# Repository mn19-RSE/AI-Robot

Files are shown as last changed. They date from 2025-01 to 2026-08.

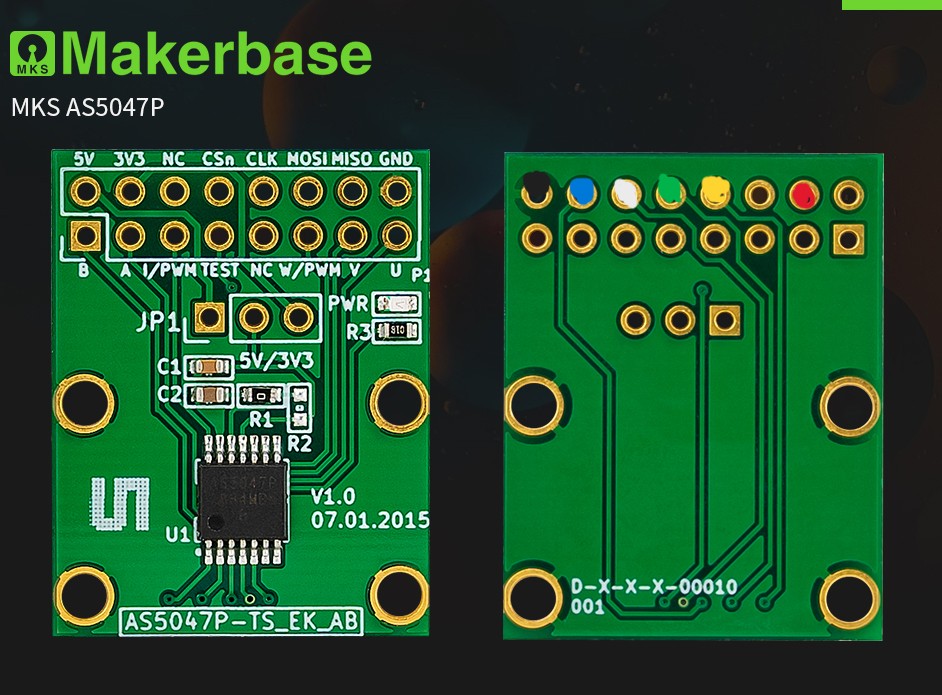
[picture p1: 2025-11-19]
hardware/reference_images/AS5047P Image.jpg

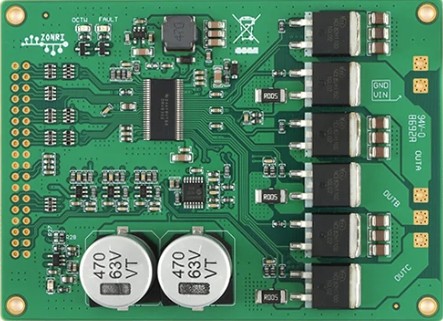
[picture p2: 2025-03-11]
hardware/reference_images/DRV8302_Top_View_Image.jpg

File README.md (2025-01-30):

# AI-Robot
This is a repo representing the personal robotics project I started in late 2024.  
The plan is to create a walking robot that will incorporate BLDC motors, CAN bus communication, machine vision, and AI models for object detection and decision making.

## License
This project is protected under the defualt copyright laws. I retain all rights to the source code created by me and no one may reproduce, distribute, or create derivative original works from this project.

## Contained Files
- 3D CAD models
- Arduino code for motion control
- ML code for machine vision and decisinon making 
- BOM

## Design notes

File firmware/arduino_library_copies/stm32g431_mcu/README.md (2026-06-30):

# STM32G431 MCU Header file library
Pin definitions for the BLDC complete drive controller that uses the STM32G431 microcontorller. SPI pins, driver PWM and enebale pins, and the CAN pins are defined to make it easier to call functions in the .ino file.

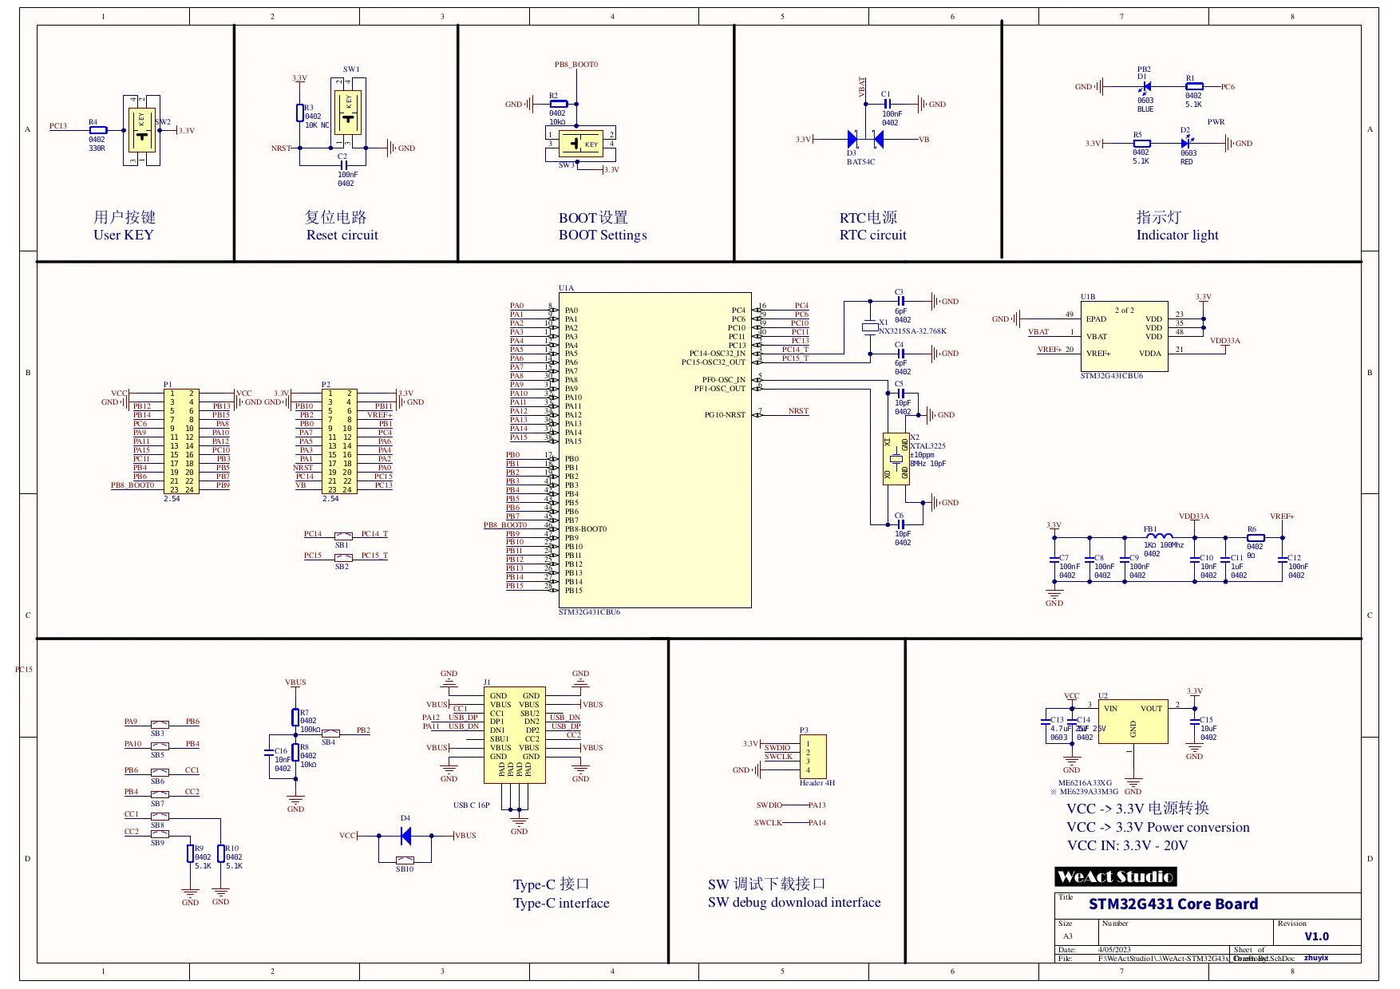
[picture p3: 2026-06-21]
hardware/electrical_documentation/schematics/WeAct-STM32G4-schematics.jpg

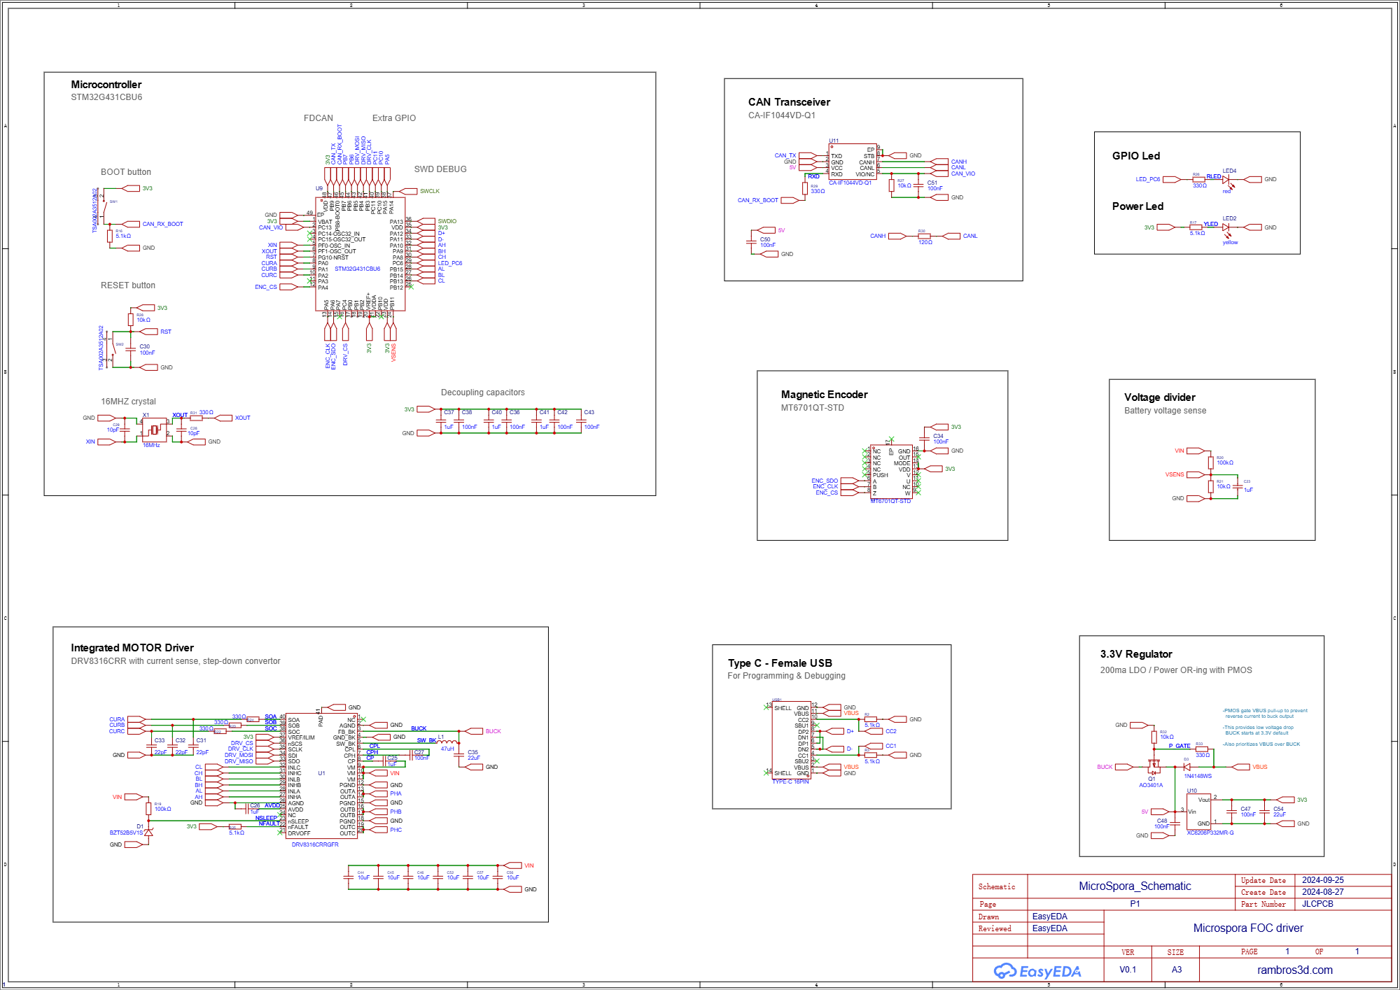
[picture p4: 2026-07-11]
hardware/electrical_documentation/schematics/SCH_MIcroSpora_DRV8316.png

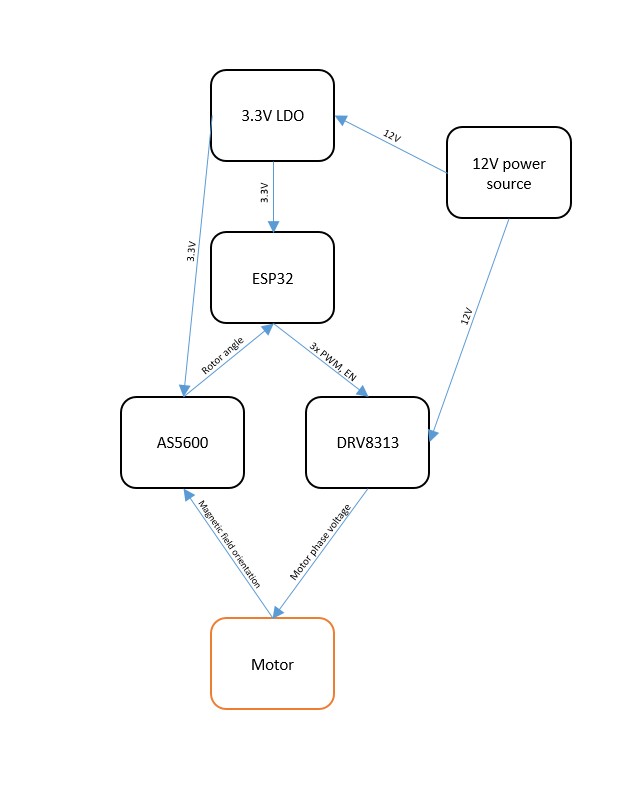
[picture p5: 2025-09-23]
hardware/reference_images/AIO_ESP32_DRV8313_AS5600_block_diagram.jpg

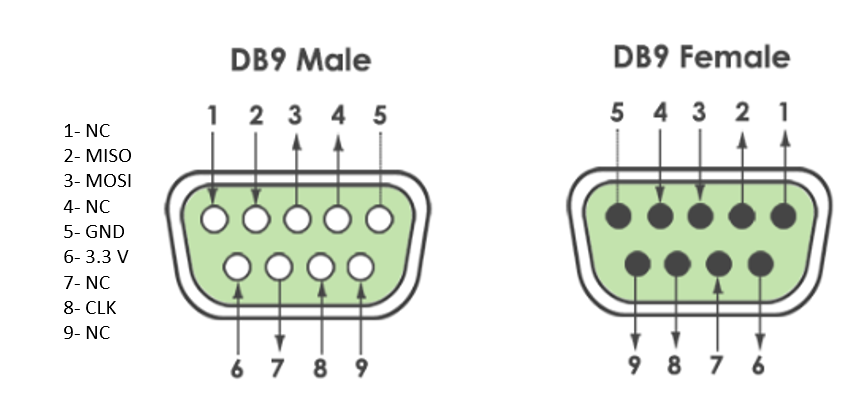
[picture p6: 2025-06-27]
hardware/reference_images/DB9 AS5047p Pinout.png

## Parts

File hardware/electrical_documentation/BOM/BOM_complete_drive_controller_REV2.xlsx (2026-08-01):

No. | Quantity | Comment | Designator | Footprint | Value | Manufacturer Part | Supplier Part | Category | Device
1 | 10 | 100nF | C1,C2,C3,C4,C5,C6,C7,C8,C9,C14 | C0402 | 100nF |  | C1525 | Capacitors:Multilayer Ceramic Capacitors MLCC - SMD/SMT | CAP_0402
2 | 4 | 100nF | C10,C11,C12,C15 | C0603 | 100nF |  |  | Capacitors:Multilayer Ceramic Capacitors MLCC - SMD/SMT | CAP_0603
3 | 1 | 47nF | C13 | C0603 | 47nF |  |  | Capacitors:Multilayer Ceramic Capacitors MLCC - SMD/SMT | CAP_0603
4 | 1 | 100nF | C16 | C0603 | 100nF | CC0603KRX7R9BB104 | C14663 | Capacitors:Multilayer Ceramic Capacitors MLCC - SMD/SMT | CC0603KRX7R9BB104
5 | 1 | 10uF | C17 | C0402 | 10uF | CL05A106MQ5NUNC | C15525 | Capacitors:Multilayer Ceramic Capacitors MLCC - SMD/SMT | CL05A106MQ5NUNC
6 | 1 | 22uF | Cbk | C0402 | 22uF |  |  | Capacitors:Multilayer Ceramic Capacitors MLCC - SMD/SMT | CAP_0402
7 | 1 | SMBJ12A | D1 | SMB_L4.6-W3.6-LS5.3-RD |  | SMBJ12A | C127552 |  | SMBJ12A
8 | 1 | HDR-M_2.54_1x2P | H1 | HDR-TH_2P-P2.54-V-M-1 |  |  |  | Connectors:Pin Headers | HDR-M_2.54_1x2P
9 | 1 | 47uH | Lbk | L0805 | 47uH |  |  | Inductors/Coils/Transformers:Inductors (SMD) | L_0805
10 | 2 | 10K | R2,R5 | R0603 | 10K |  |  | Resistors:Chip Resistor - Surface Mount | Res_0603
11 | 1 | 5.1K | R6 | R0402 | 5.1K |  |  | Resistors:Chip Resistor - Surface Mount | Res_0402
12 | 1 | 47K | R7 | R0402 | 47K |  |  | Resistors:Chip Resistor - Surface Mount | Res_0402
13 | 1 | 10kΩ | R8 | R0603 | 10kΩ | 0603WAF1002T5E | C25804 | Resistors:Chip Resistor - Surface Mount | 0603WAF1002T5E
14 | 2 | 5.1K | R9,R10 | R0603 | 5.1K |  |  | Resistors:Chip Resistor - Surface Mount | Res_0603
15 | 1 | 120 | RCAN | R0603 | 120 |  |  | Resistors:Chip Resistor - Surface Mount | Res_0603
16 | 2 | 95c04a3gwrt | S1,S2 | 95C04A3GWRT | 95C04A3GWRT |  |  |  | 95c04a3gwrt
17 | 1 | STM32G431CBT6 | U2 | LQFP-48_L7.0-W7.0-P0.50-LS9.0-BL |  | STM32G431CBT6 | C529355 | Embedded Processors & Controllers:Microcontrollers (MCU/MPU/SOC) | STM32G431CBT6
18 | 1 | DRV8316CTRGFR | U3 | VQFN-40_L7.0-W5.0-P0.50-TL-EP5.7 |  | DRV8316CTRGFR | C6602057 | Motor Driver ICs:Brushless DC (BLDC) Motor Driver | DRV8316CTRGFR
19 | 1 | aha0608470m035r | U4 | CAPAE660X850N |  |  |  |  | aha0608470m035r
20 | 1 | AS5048A-HTSP-500 | U5 | TSSOP-14_L5.0-W4.4-P0.65-LS6.4-BL |  | AS5048A-HTSP-500 | C2655181 | Sensors:Position Sensors | AS5048A-HTSP-500
21 | 1 | XT30(2+2) | U6 | CONN-TH_XT30-2-2 |  | XT30(2+2) | C9900178769 |  | XT30(2+2)
22 | 1 | CONN_03_POS_SCREW_3.5MM | U7 | SCREWTERMINAL-3.5MM-3 |  |  |  |  | CONN_03_POS_SCREW_3.5MM
23 | 1 | TCAN3413DR | U8 | SOP-8_L4.9-W3.9-P1.27-LS6.0-BL-1 |  | TCAN3413DR | C22433320 | Interface:CAN Transceivers | TCAN3413DR
24 | 1 | USB4120-03-C | USB1 | TYPE-C-SMD_USB4120-03-C |  | USB4120-03-C | C3445864 | Connectors:USB Connectors | USB4120-03-C

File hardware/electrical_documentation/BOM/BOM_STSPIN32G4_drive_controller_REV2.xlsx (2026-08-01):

No. | Quantity | Comment | Designator | Footprint | Value | Manufacturer Part | Manufacturer | Supplier Part | Supplier | Category | Device
1 | 8 | 100nF | C1,C3,C5,C9,C11,C12,C13,C15 | C0603 | 100nF |  |  |  |  | Capacitors:Multilayer Ceramic Capacitors MLCC - SMD/SMT | CAP_0603
2 | 2 | 1uF | C2,C4 | C0603 | 1uF |  |  |  |  | Capacitors:Multilayer Ceramic Capacitors MLCC - SMD/SMT | CAP_0603
3 | 2 | 10uF | C6,C10 | C0603 | 10uF |  |  |  |  | Capacitors:Multilayer Ceramic Capacitors MLCC - SMD/SMT | CAP_0603
4 | 2 | 100nF | C7,C8 | C0402 | 100nF |  |  | C1525 |  | Capacitors:Multilayer Ceramic Capacitors MLCC - SMD/SMT | CAP_0402
5 | 1 | 10uF | C14 | C0603 | 10uF | CC0603KRX7R9BB104 | YAGEO(国巨) |  | LCSC | Capacitors:Multilayer Ceramic Capacitors MLCC - SMD/SMT | CC0603KRX7R9BB104
6 | 1 | 100nF | C16 | C0603 | 100nF | CC0603KRX7R9BB104 | YAGEO(国巨) | C14663 | LCSC | Capacitors:Multilayer Ceramic Capacitors MLCC - SMD/SMT | CC0603KRX7R9BB104
7 | 1 | STPS1H100A | D1 | SMA_L4.3-W2.6-LS5.2-RD |  | STPS1H100A | ST(意法半导体) | C165701 | LCSC | Diodes:Schottky Diodes | STPS1H100A
8 | 1 | HDR-M_2.54_1x2P | H1 | HDR-TH_2P-P2.54-V-M-1 |  |  |  |  |  | Connectors:Pin Headers | HDR-M_2.54_1x2P
9 | 1 | 15uH | L2 | IND-SMD_L3.8-W3.8_74406032010 | 15uH | SRR3818A-150M | BOURNS | C2045035 | LCSC | Inductors, Coils, Chokes:Power Inductors | SRR3818A-150M
10 | 3 | CSD88584Q5DC | M1,M2,M3 | SON-22_L5.0-W6.0-P0.50-CSD88599Q5DCT |  | CSD88584Q5DC | TI(德州仪器) | C2683056 | LCSC | Power Modules:DC-DC Power Modules | CSD88584Q5DC
11 | 2 | 10K | R1,R2 | R0603 | 10K |  |  |  |  | Resistors:Chip Resistor - Surface Mount | Res_0603
12 | 2 | 5.1K | R3,R4 | R0603 | 5.1K |  |  |  |  | Resistors:Chip Resistor - Surface Mount | Res_0603
13 | 6 | 4.7 | R5,R6,R7,R8,R9,R10 | R0603 | 4.7 |  |  |  |  | Resistors:Chip Resistor - Surface Mount | Res_0603
14 | 6 | 100K | R11,R12,R13,R14,R15,R16 | R0402 | 100K |  |  |  |  | Resistors:Chip Resistor - Surface Mount | Res_0402
15 | 1 | 10kΩ | R17 | R0603 | 10kΩ | 0603WAF1002T5E | UNI-ROYAL(厚声) | C25804 | LCSC | Resistors:Chip Resistor - Surface Mount | 0603WAF1002T5E
16 | 1 | 120 | RCAN | R0603 | 120 |  |  |  |  | Resistors:Chip Resistor - Surface Mount | Res_0603
17 | 2 | 95c04a3gwrt | S1,S2 | 95C04A3GWRT | 95C04A3GWRT |  |  |  |  |  | 95c04a3gwrt
18 | 1 | STSPIN32G4 | U1 | VFQFPN-64_L9.0-W9.0-P0.50-TL-EP4.0 |  | STSPIN32G4 | ST(意法半导体) | C2858620 | LCSC | Transistors/Thyristors:Intelligent Power Modules (IPM) | STSPIN32G4
19 | 1 | aha0608470m035r | U2 | CAPAE660X850N |  |  |  |  |  |  | aha0608470m035r
20 | 1 | AS5048A-HTSP-500 | U5 | TSSOP-14_L5.0-W4.4-P0.65-LS6.4-BL |  | AS5048A-HTSP-500 | ams(艾迈斯半导体) | C2655181 | LCSC | Sensors:Position Sensors | AS5048A-HTSP-500
21 | 1 | TCAN3413DR | U8 | SOP-8_L4.9-W3.9-P1.27-LS6.0-BL-1 |  | TCAN3413DR | TI(德州仪器) | C22433320 | LCSC | Interface:CAN Transceivers | TCAN3413DR
22 | 1 | USB4120-03-C | USB1 | TYPE-C-SMD_USB4120-03-C |  | USB4120-03-C | GCT | C3445864 | LCSC | Connectors:USB Connectors | USB4120-03-C

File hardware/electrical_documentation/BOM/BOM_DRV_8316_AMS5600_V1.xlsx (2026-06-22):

No. | Quantity | Comment | Designator | Footprint | Value | Manufacturer Part | Manufacturer | Supplier Part | Supplier
1 | 2 | 1uF | Ca,Cp | C0603 | 1uF
2 | 1 | 47uF | Cb | CAPAE660X850N
3 | 1 | 47nF | Cd | C0603 | 47nF
4 | 1 | 100nF | Ce | C0603 | 100nF
5 | 1 | .1uF | Cr | C0603 | .1uF
6 | 5 | 10uF | Cri,Cro,Cv0,Cv1,Cv2 | C0603 | 10uF
7 | 2 | 2.54-1*5P母 | H1,H4 | HDR-TH_5P-P2.54-V-F |  | 2.54-1*5P母 | BOOMELE(博穆精密) | C50950 | LCSC
8 | 1 | HDR-F_2.54_1x3P | H3 | HDR-TH_3P-P2.54-V-F
9 | 2 | 4.7K | R1,R2 | R0603 | 4.7K
10 | 3 | 22 | R3,R4,R5 | R0603 | 22
11 | 2 | 10K | Rf,Rm | R0603 | 10K
12 | 1 | AS5600-ASOM | U1 | SOIC127P600X175-8N
13 | 1 | ncp1117idt33t4g | U2 | NCP1117IDT33T4G
14 | 1 | DRV8316CTRGFR | U3 | VQFN-40_L7.0-W5.0-P0.50-TL-EP5.7 |  | DRV8316CTRGFR | TI(德州仪器) | C6602057 | LCSC
15 | 1 | sd12c.tct | U4 | SD12CTCT

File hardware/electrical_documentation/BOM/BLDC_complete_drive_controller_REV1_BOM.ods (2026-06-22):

No. | Quantity | Comment | Designator | Footprint | Value | Manufacturer Part | Manufacturer | Supplier Part | Supplier
1 | 10 | 100nF | C1,C2,C3,C4,C5,C6,C7,C8,C9,C14 | C0402 | 100nF |  |  | C1525
2 | 4 | 100nF | C10,C11,C12,C15 | C0603 | 100nF
3 | 1 | 47nF | C13 | C0603 | 47nF
4 | 1 | 100nF | C16 | C0603 | 100nF | CC0603KRX7R9BB104 | YAGEO(国巨) | C14663 | LCSC
5 | 1 | 10uF | C17 | C0402 | 10uF | CL05A106MQ5NUNC | SAMSUNG(三星) | C15525 | LCSC
6 | 1 | 22uF | Cbk | C0402 | 22uF
7 | 1 | HDR-M_2.54_1x4P | H1 | HDR-TH_4P-P2.54-V-M
8 | 1 | HDR-M_2.54_1x3P | H4 | HDR-TH_3P-P2.54-V-M
9 | 1 | 47uH | Lbk | L0805 | 47uH
10 | 1 | 120 | R1 | R0402 | 120
11 | 2 | 10K | R2,R5 | R0603 | 10K
12 | 2 | 5.1K | R3,R4 | R0603 | 5.1K
13 | 1 | 5.1K | R6 | R0402 | 5.1K
14 | 1 | 47K | R7 | R0402 | 47K
15 | 1 | 10kΩ | R8 | R0603 | 10kΩ | 0603WAF1002T5E | UNI-ROYAL(厚声) | C25804 | LCSC
16 | 2 | 95c04a3gwrt | S1,S2 | 95C04A3GWRT | 95C04A3GWRT
17 | 1 | TCAN332D | U1 | SOIC-8_L4.9-W3.9-P1.27-LS6.0-BL |  | TCAN332D | TI(德州仪器) | C1544505 | LCSC
18 | 1 | STM32G431CBT6 | U2 | LQFP-48_L7.0-W7.0-P0.50-LS9.0-BL |  | STM32G431CBT6 | ST(意法半导体) | C529355 | LCSC
19 | 1 | DRV8316CTRGFR | U3 | VQFN-40_L7.0-W5.0-P0.50-TL-EP5.7 |  | DRV8316CTRGFR | TI(德州仪器) | C6602057 | LCSC
20 | 1 | aha0608470m035r | U4 | CAPAE660X850N
21 | 1 | AS5048A-HTSP-500 | U5 | TSSOP-14_L5.0-W4.4-P0.65-LS6.4-BL |  | AS5048A-HTSP-500 | ams(艾迈斯半导体) | C2655181 | LCSC
22 | 1 | USB4105-GF-A | USB_C1 | 640-USB4105-GF-A_FOOTPRINT |  | USB4105-GF-A | GCT | 640-USB4105-GF-A | Mouser

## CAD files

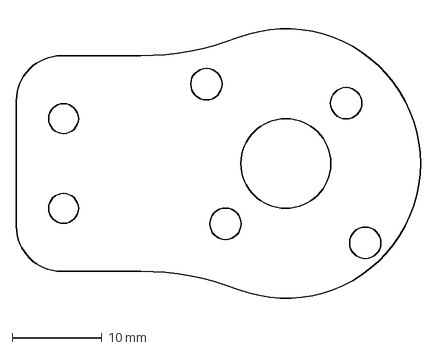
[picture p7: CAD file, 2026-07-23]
hardware/cad_models/metal_motor_mount_v2.dxf
46.0 x 32.8 mm

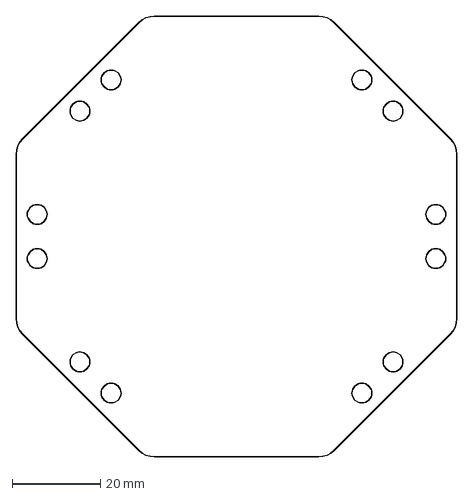
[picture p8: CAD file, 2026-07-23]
hardware/cad_models/hex_body_V1.dxf
100.0 x 100.0 mm

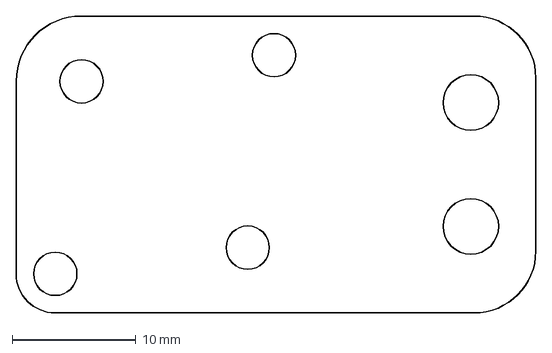
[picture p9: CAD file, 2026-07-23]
hardware/cad_models/metal_pcb_mount_v2.dxf
42.0 x 24.0 mm

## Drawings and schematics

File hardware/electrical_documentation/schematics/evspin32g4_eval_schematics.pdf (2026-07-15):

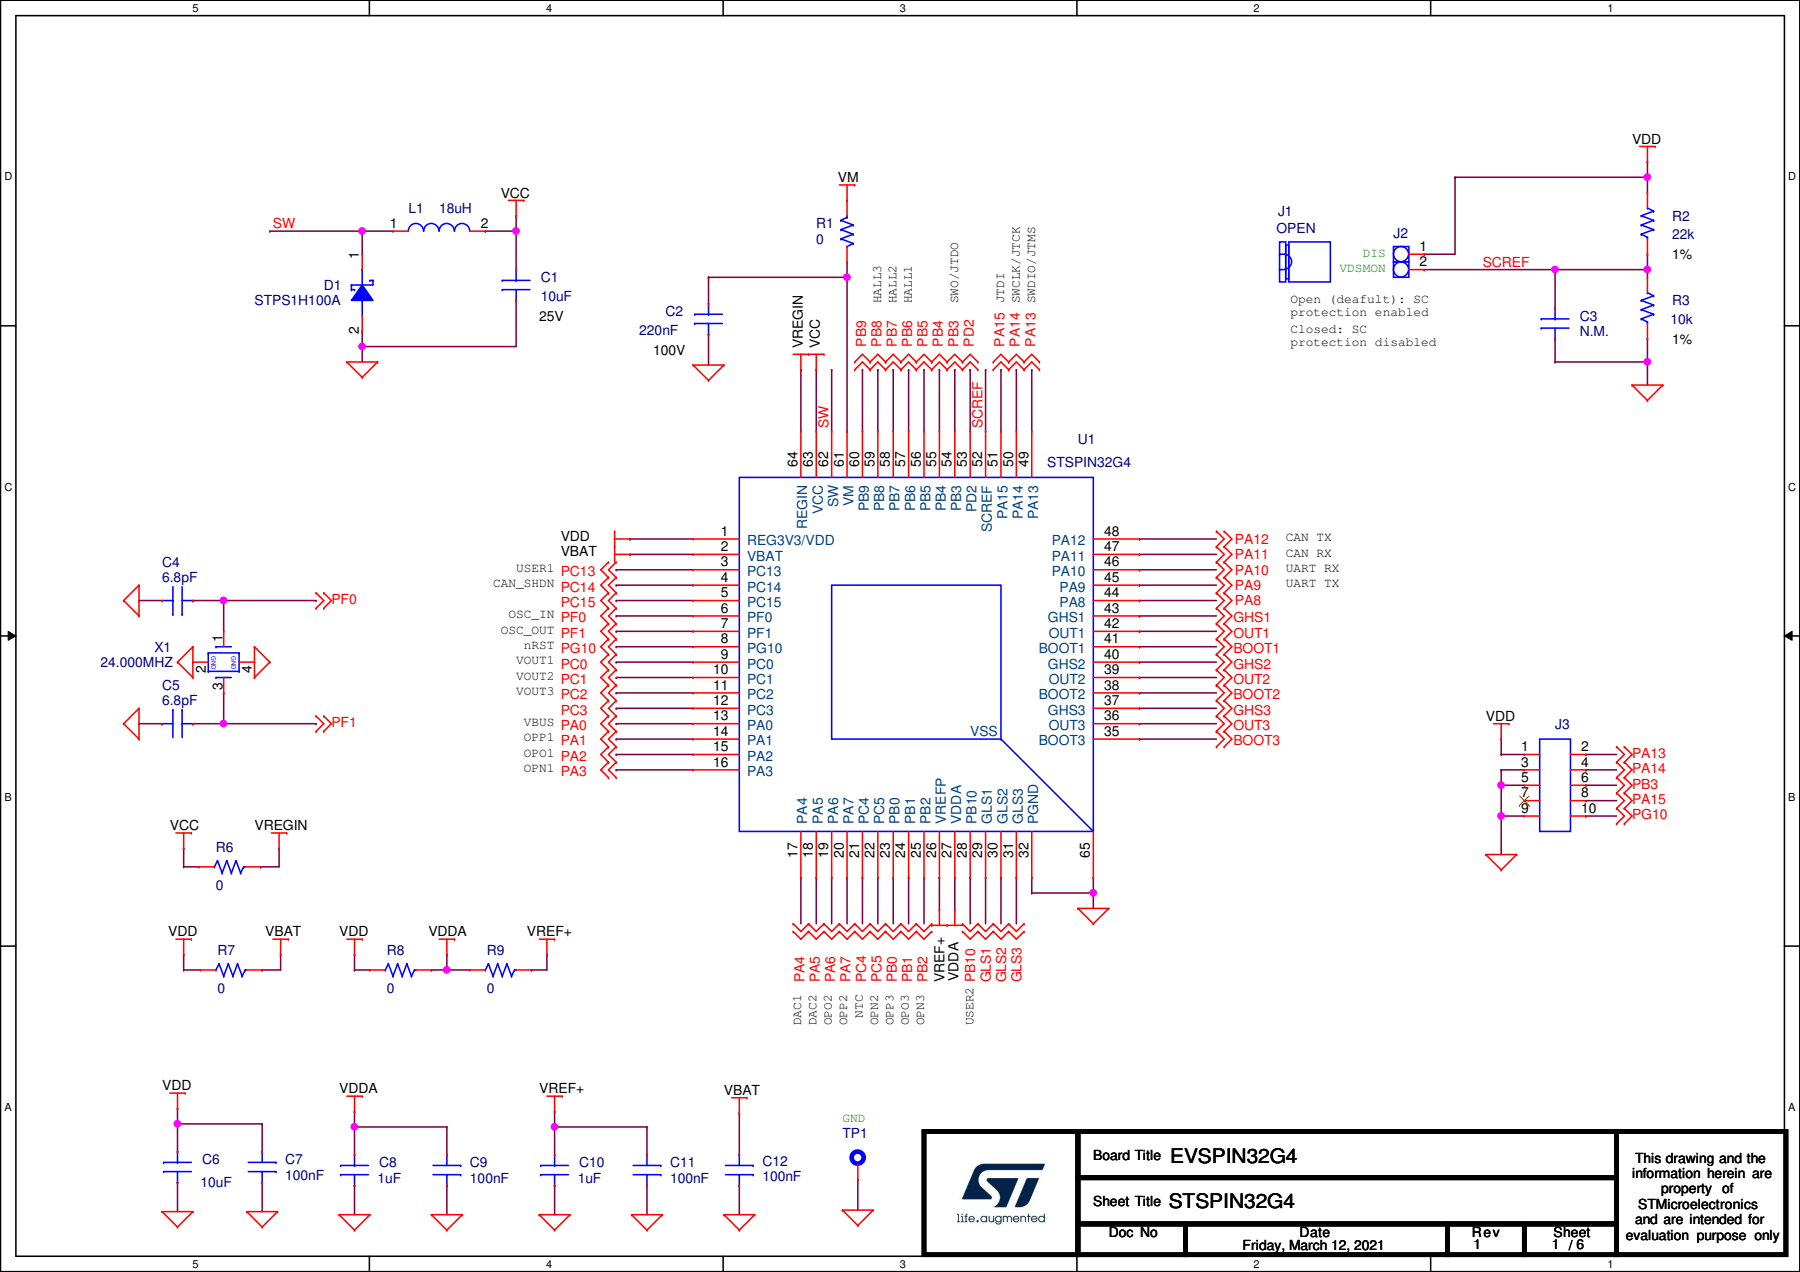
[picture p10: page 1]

This drawing and the

information herein are
property of
STMicroelectronics
and are intended for
evaluation purpose only

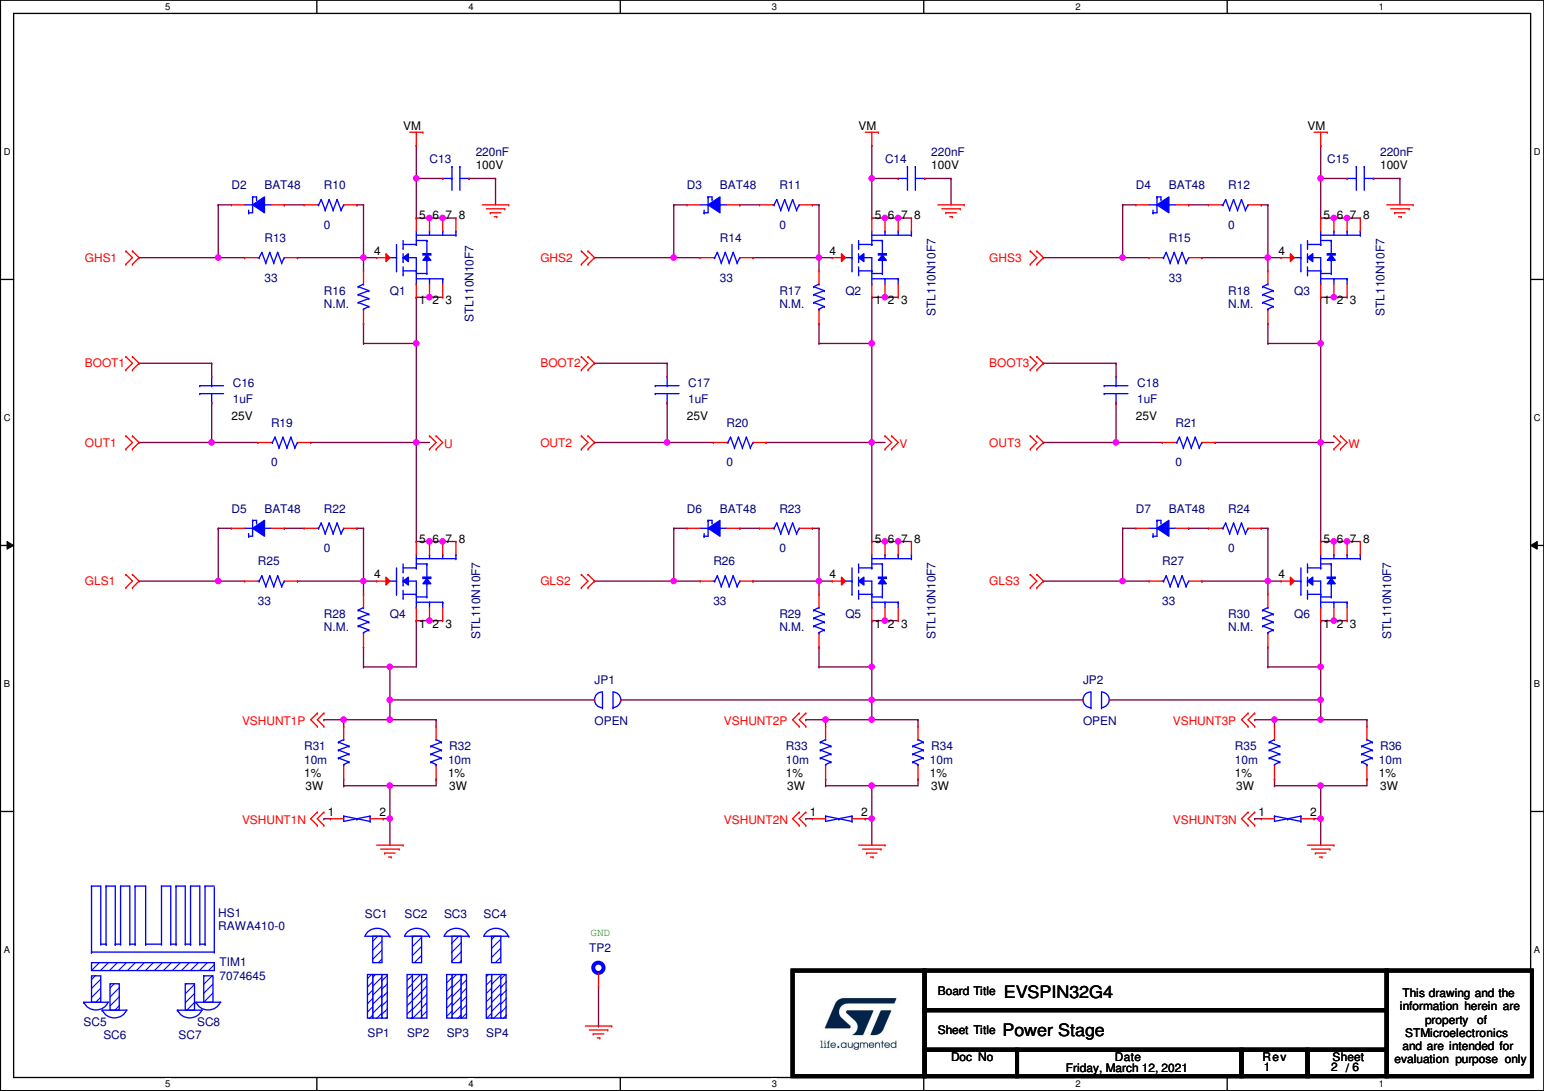
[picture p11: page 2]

This drawing and the

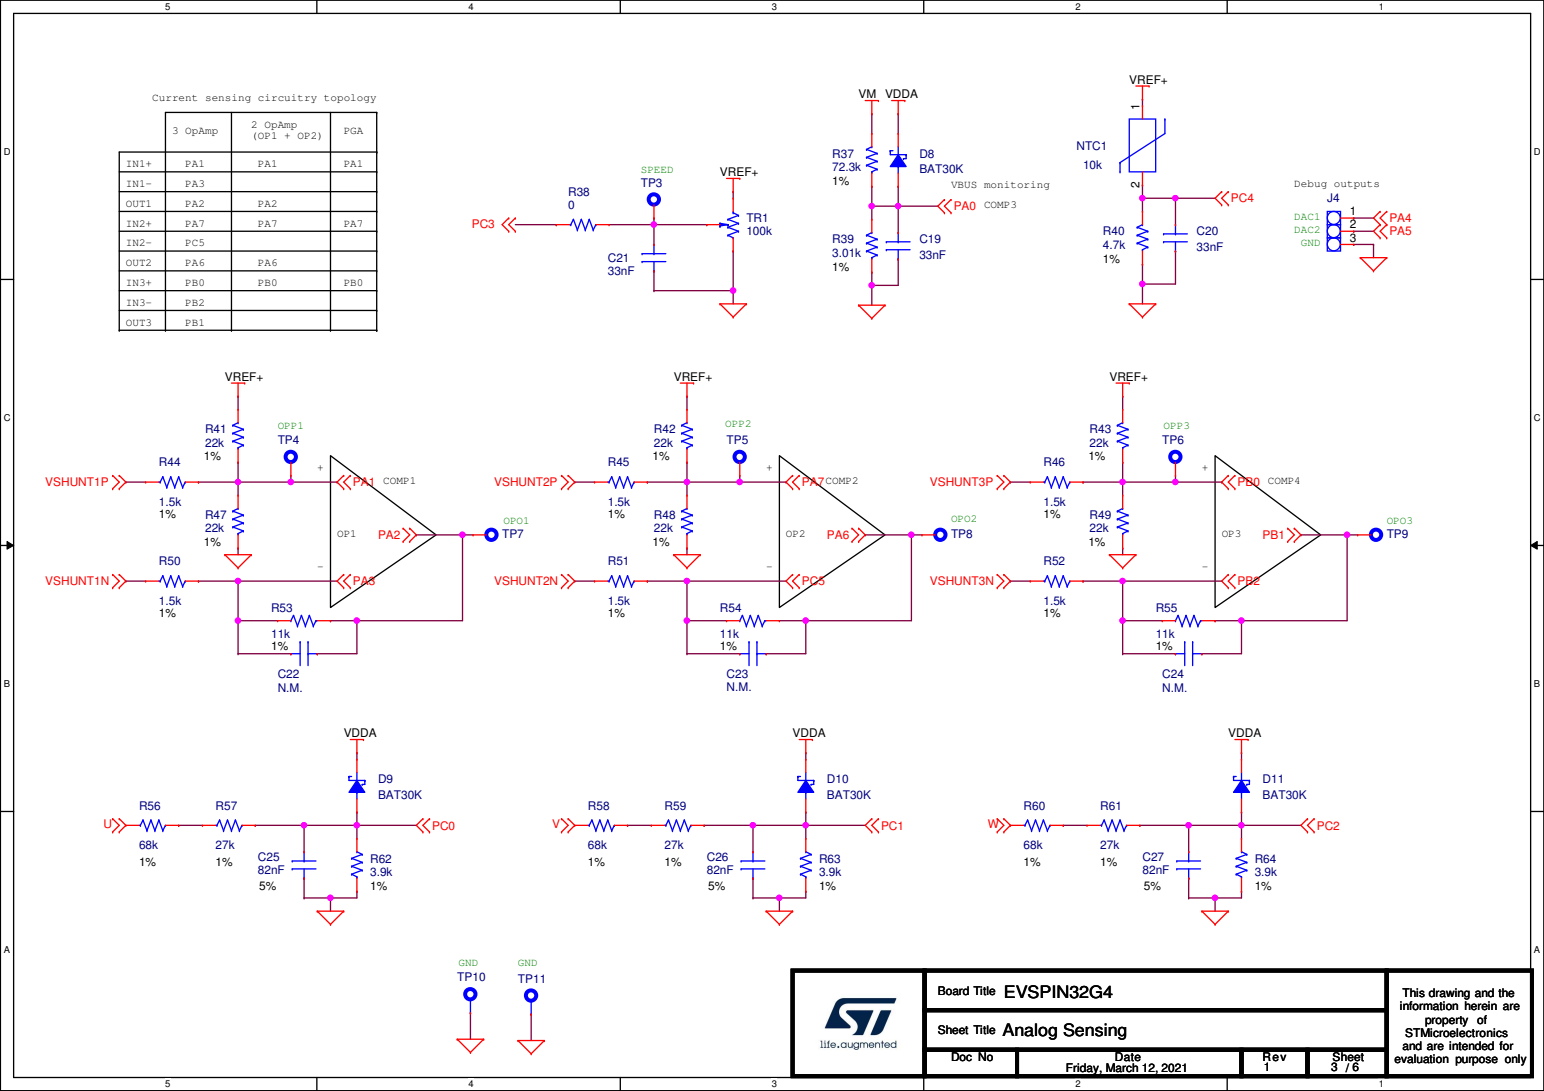
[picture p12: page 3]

VREF+

Current sensing circuitry topology

3 OpAmp | 2 OpAmp (OP1 + OP2) | PGA

OUT1 | PA2 | PA2

OUT2 | PA6 | PA6

OUT3 | PB1

This drawing and the

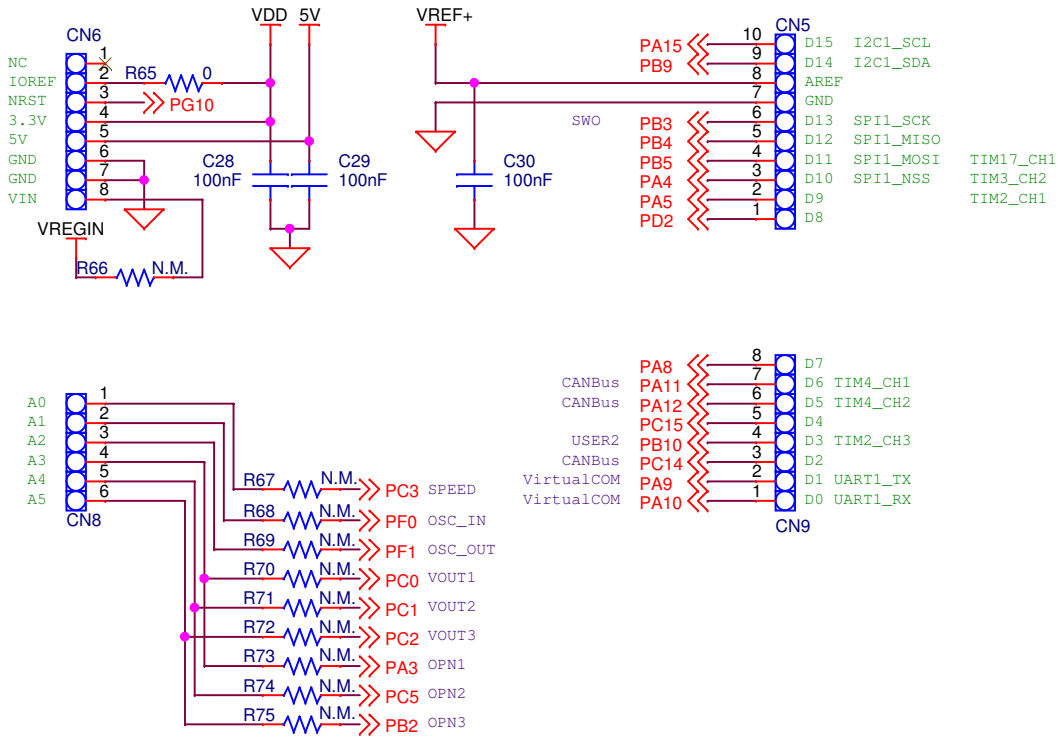
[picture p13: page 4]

This drawing and the

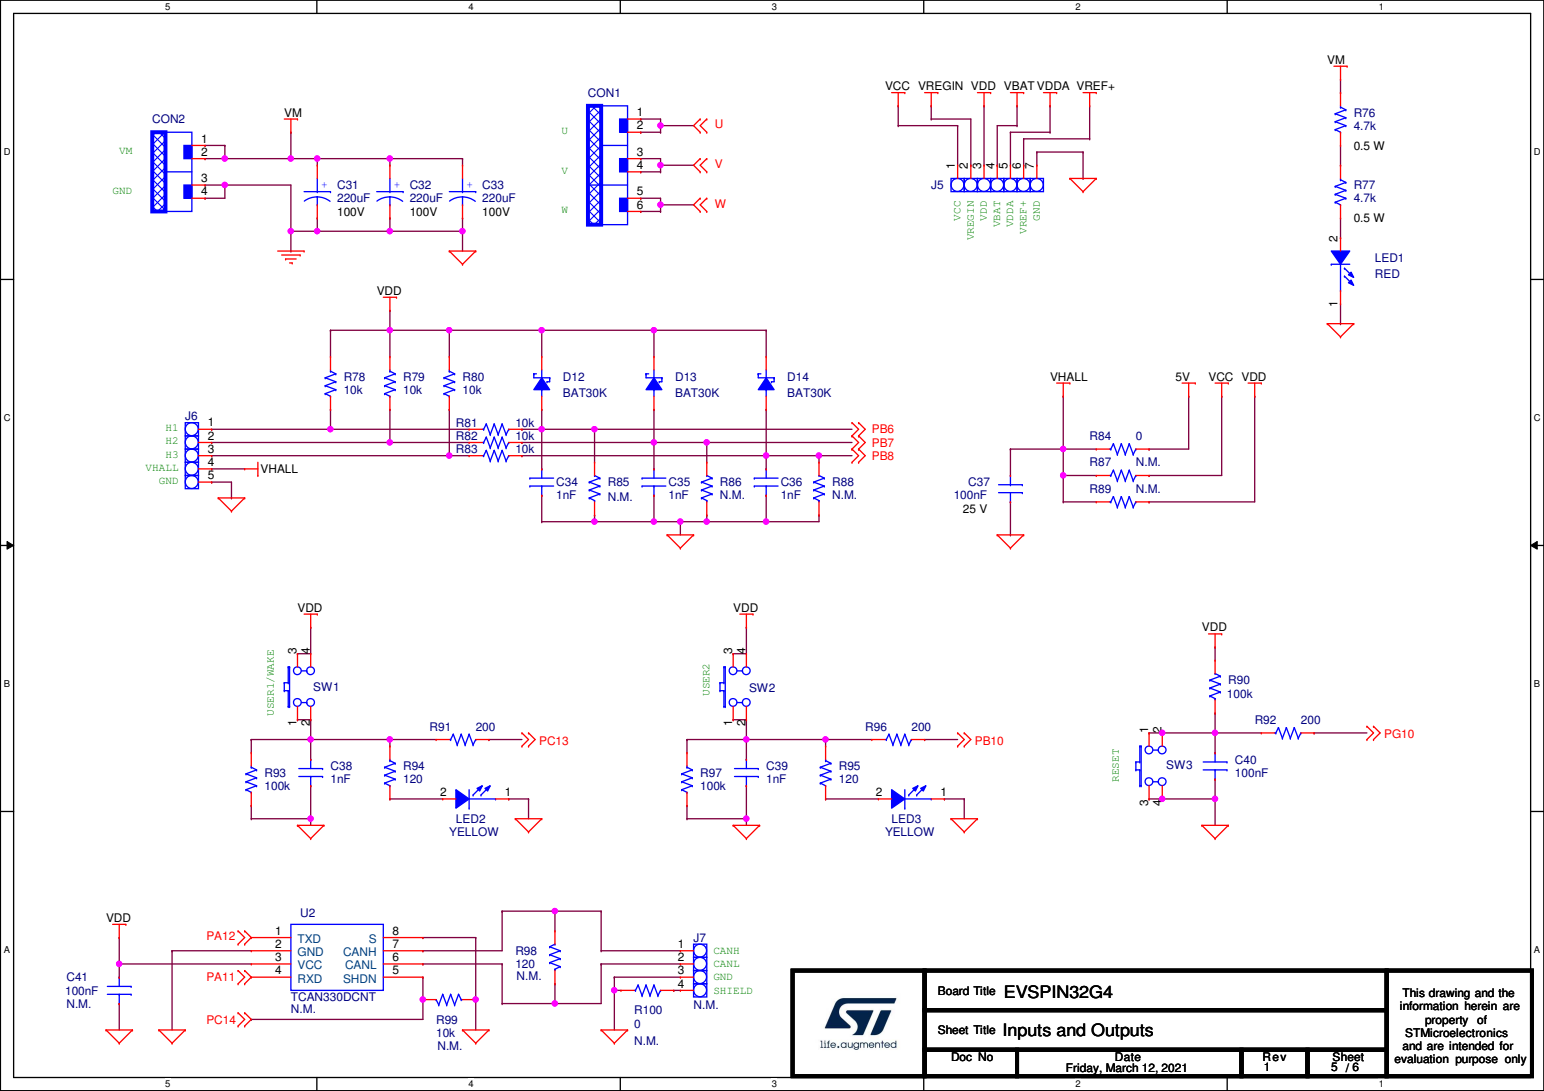
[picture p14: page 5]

VCC VREGIN VDD VBATVDDA VREF+

This drawing and the

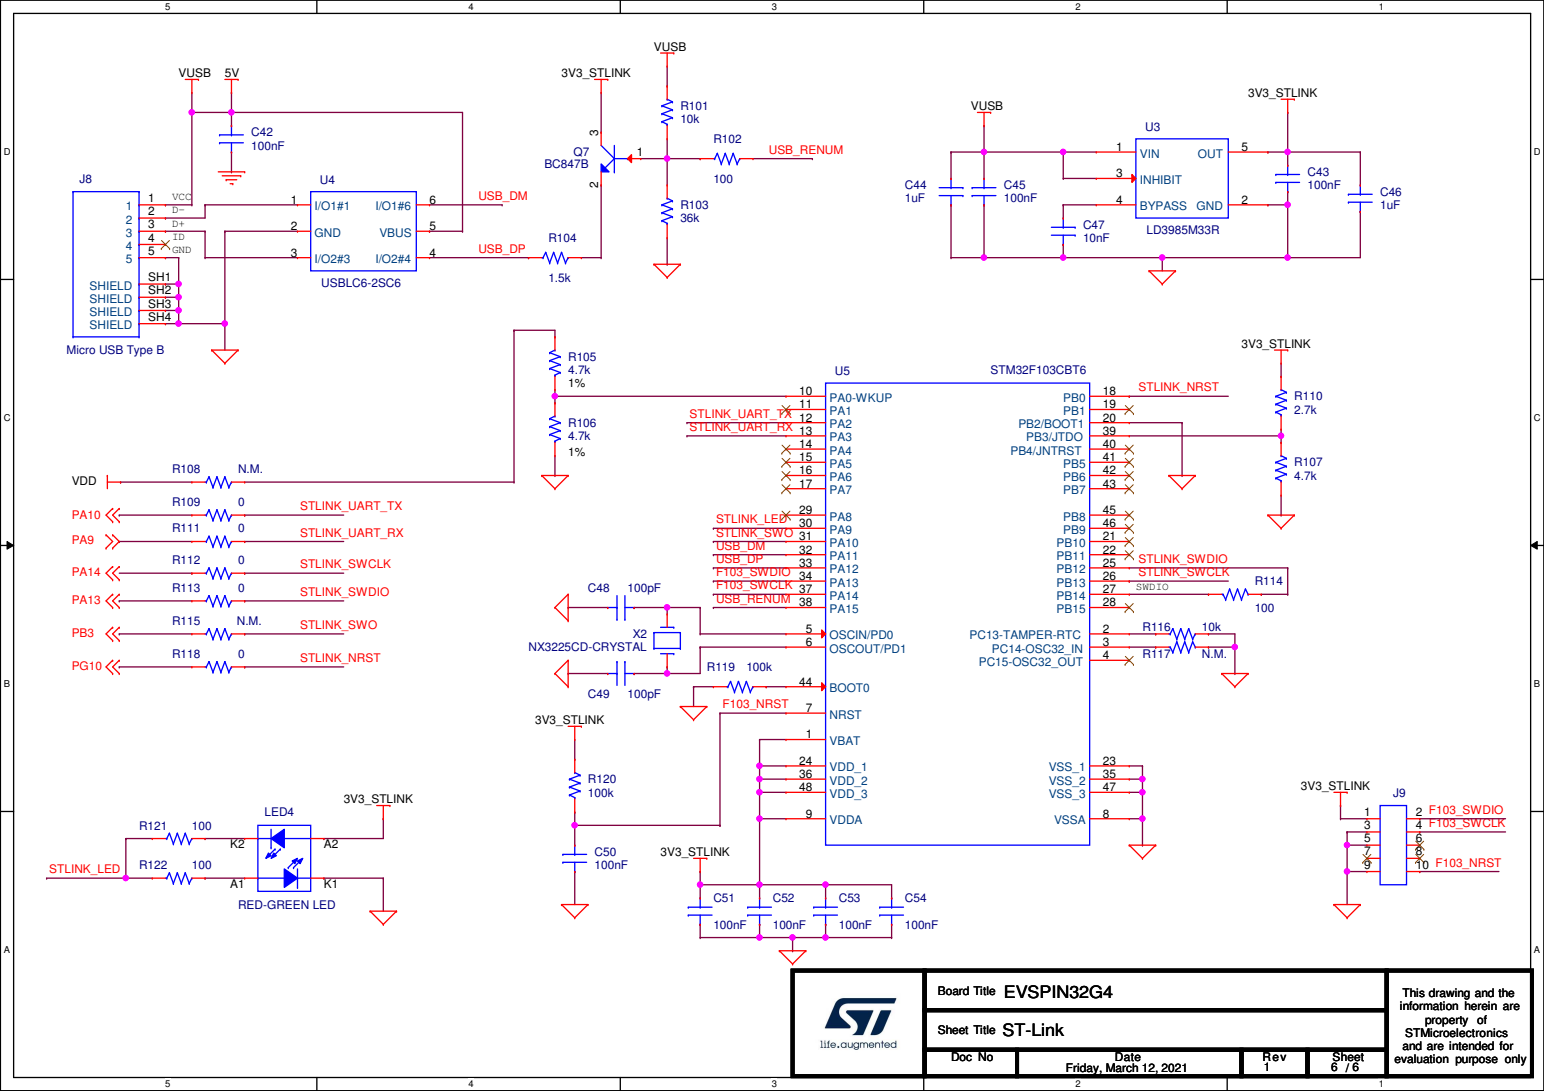
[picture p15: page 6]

This drawing and the

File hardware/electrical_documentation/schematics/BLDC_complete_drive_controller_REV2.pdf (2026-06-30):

R8

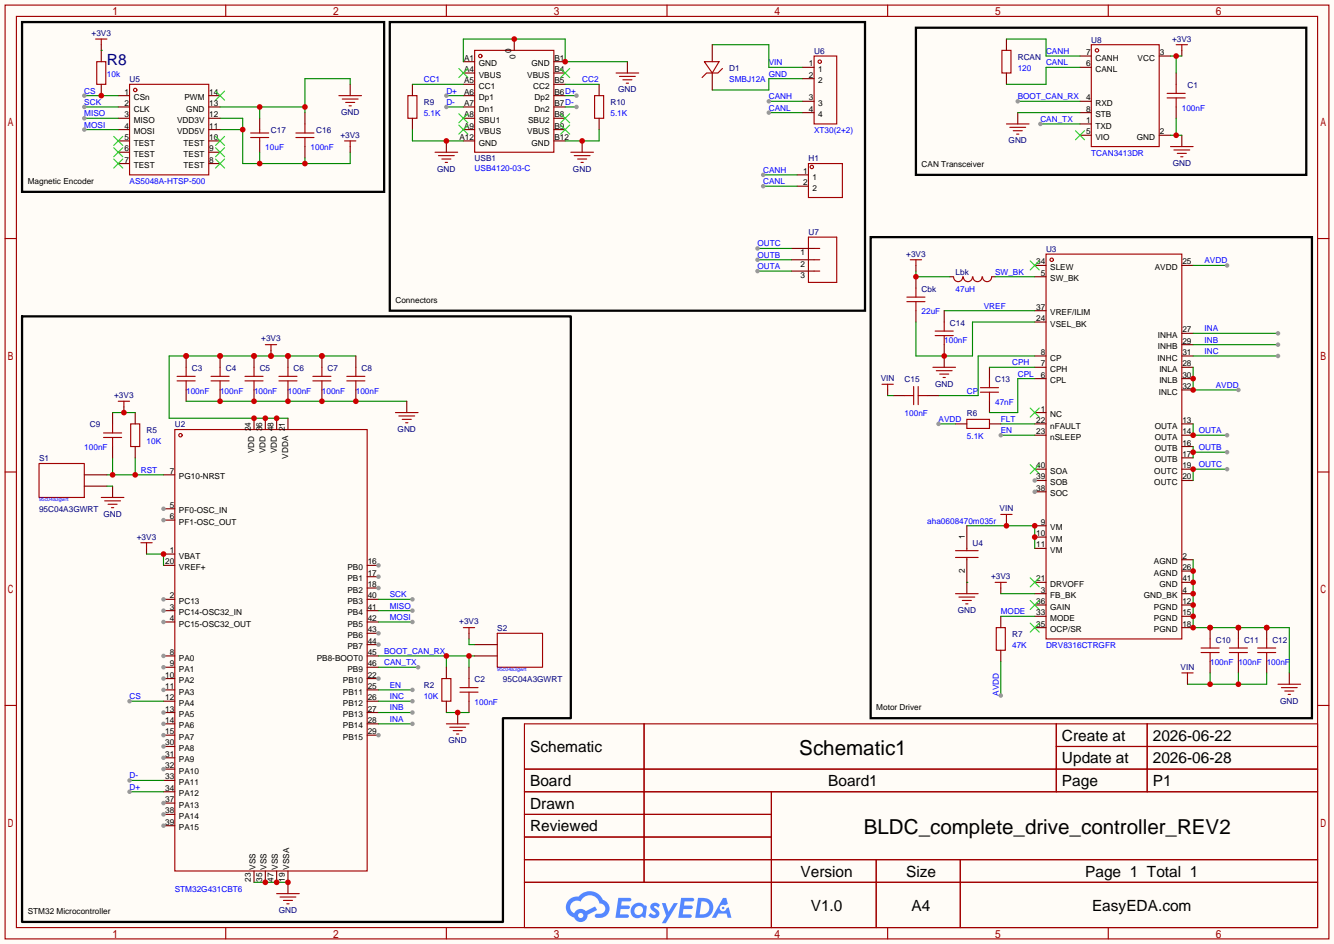
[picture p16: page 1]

INA
INLC 32 INLB 30 INLA 28 INHC 31 INHB 29 INHA 27

OUTC 20 OUTC 19 OUTB 17 OUTB 16 OUTA 14 OUTA 13

Schematic | Schematic1 | Create at | 2026-06-22

Update at | 2026-06-28

Board | Board1 | Page | P1
Drawn | | BLDC_complete_drive_controller_REV2
Reviewed

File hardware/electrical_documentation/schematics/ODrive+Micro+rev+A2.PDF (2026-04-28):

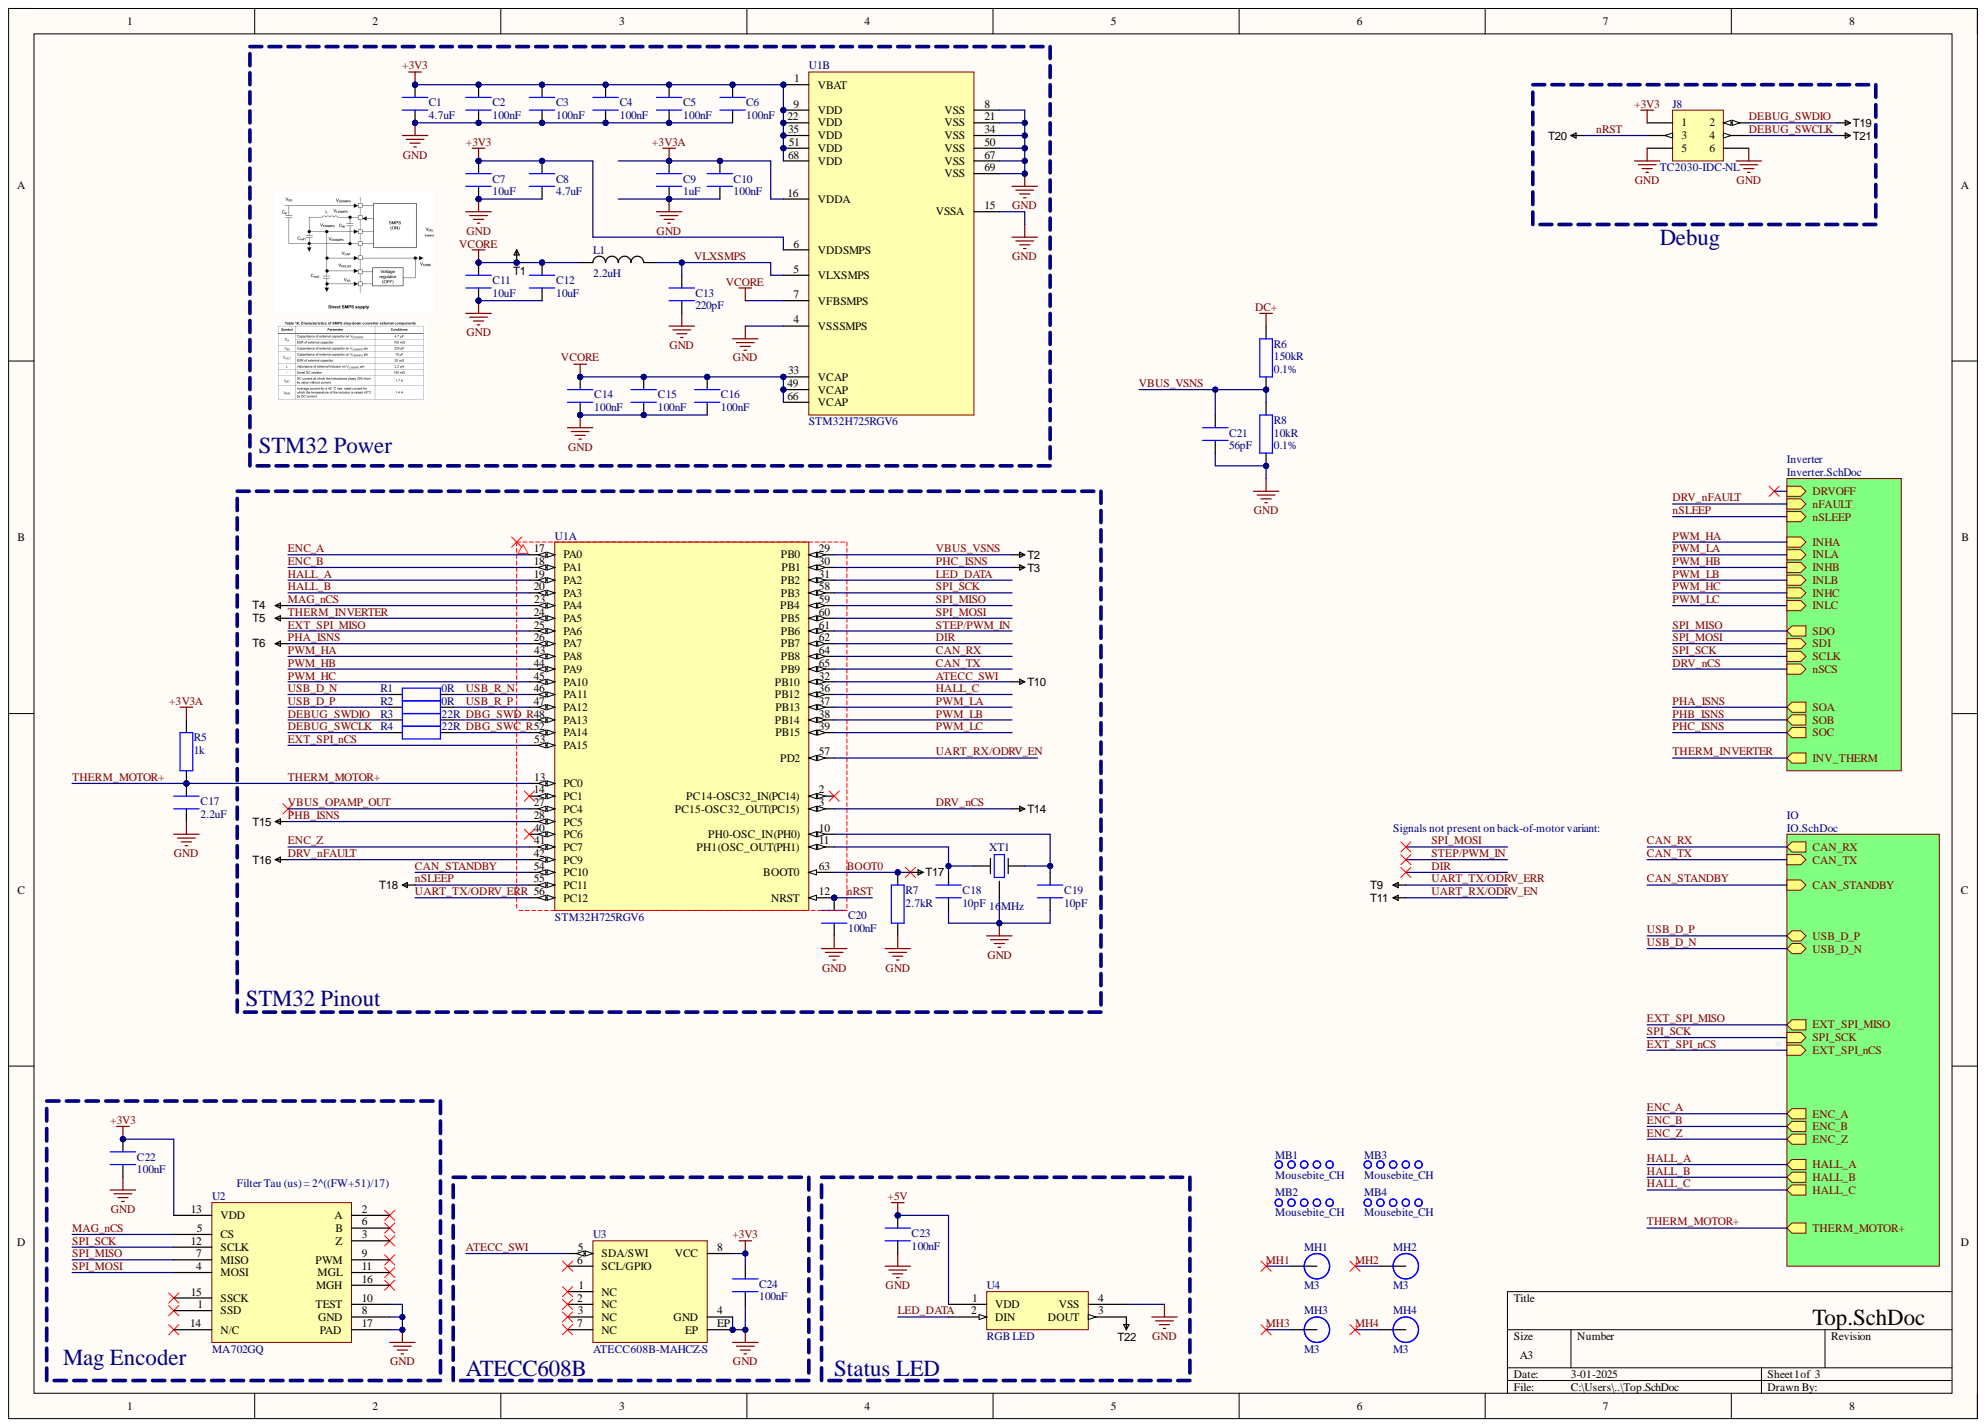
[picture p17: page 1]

Signals not present on back-of-motor variant:

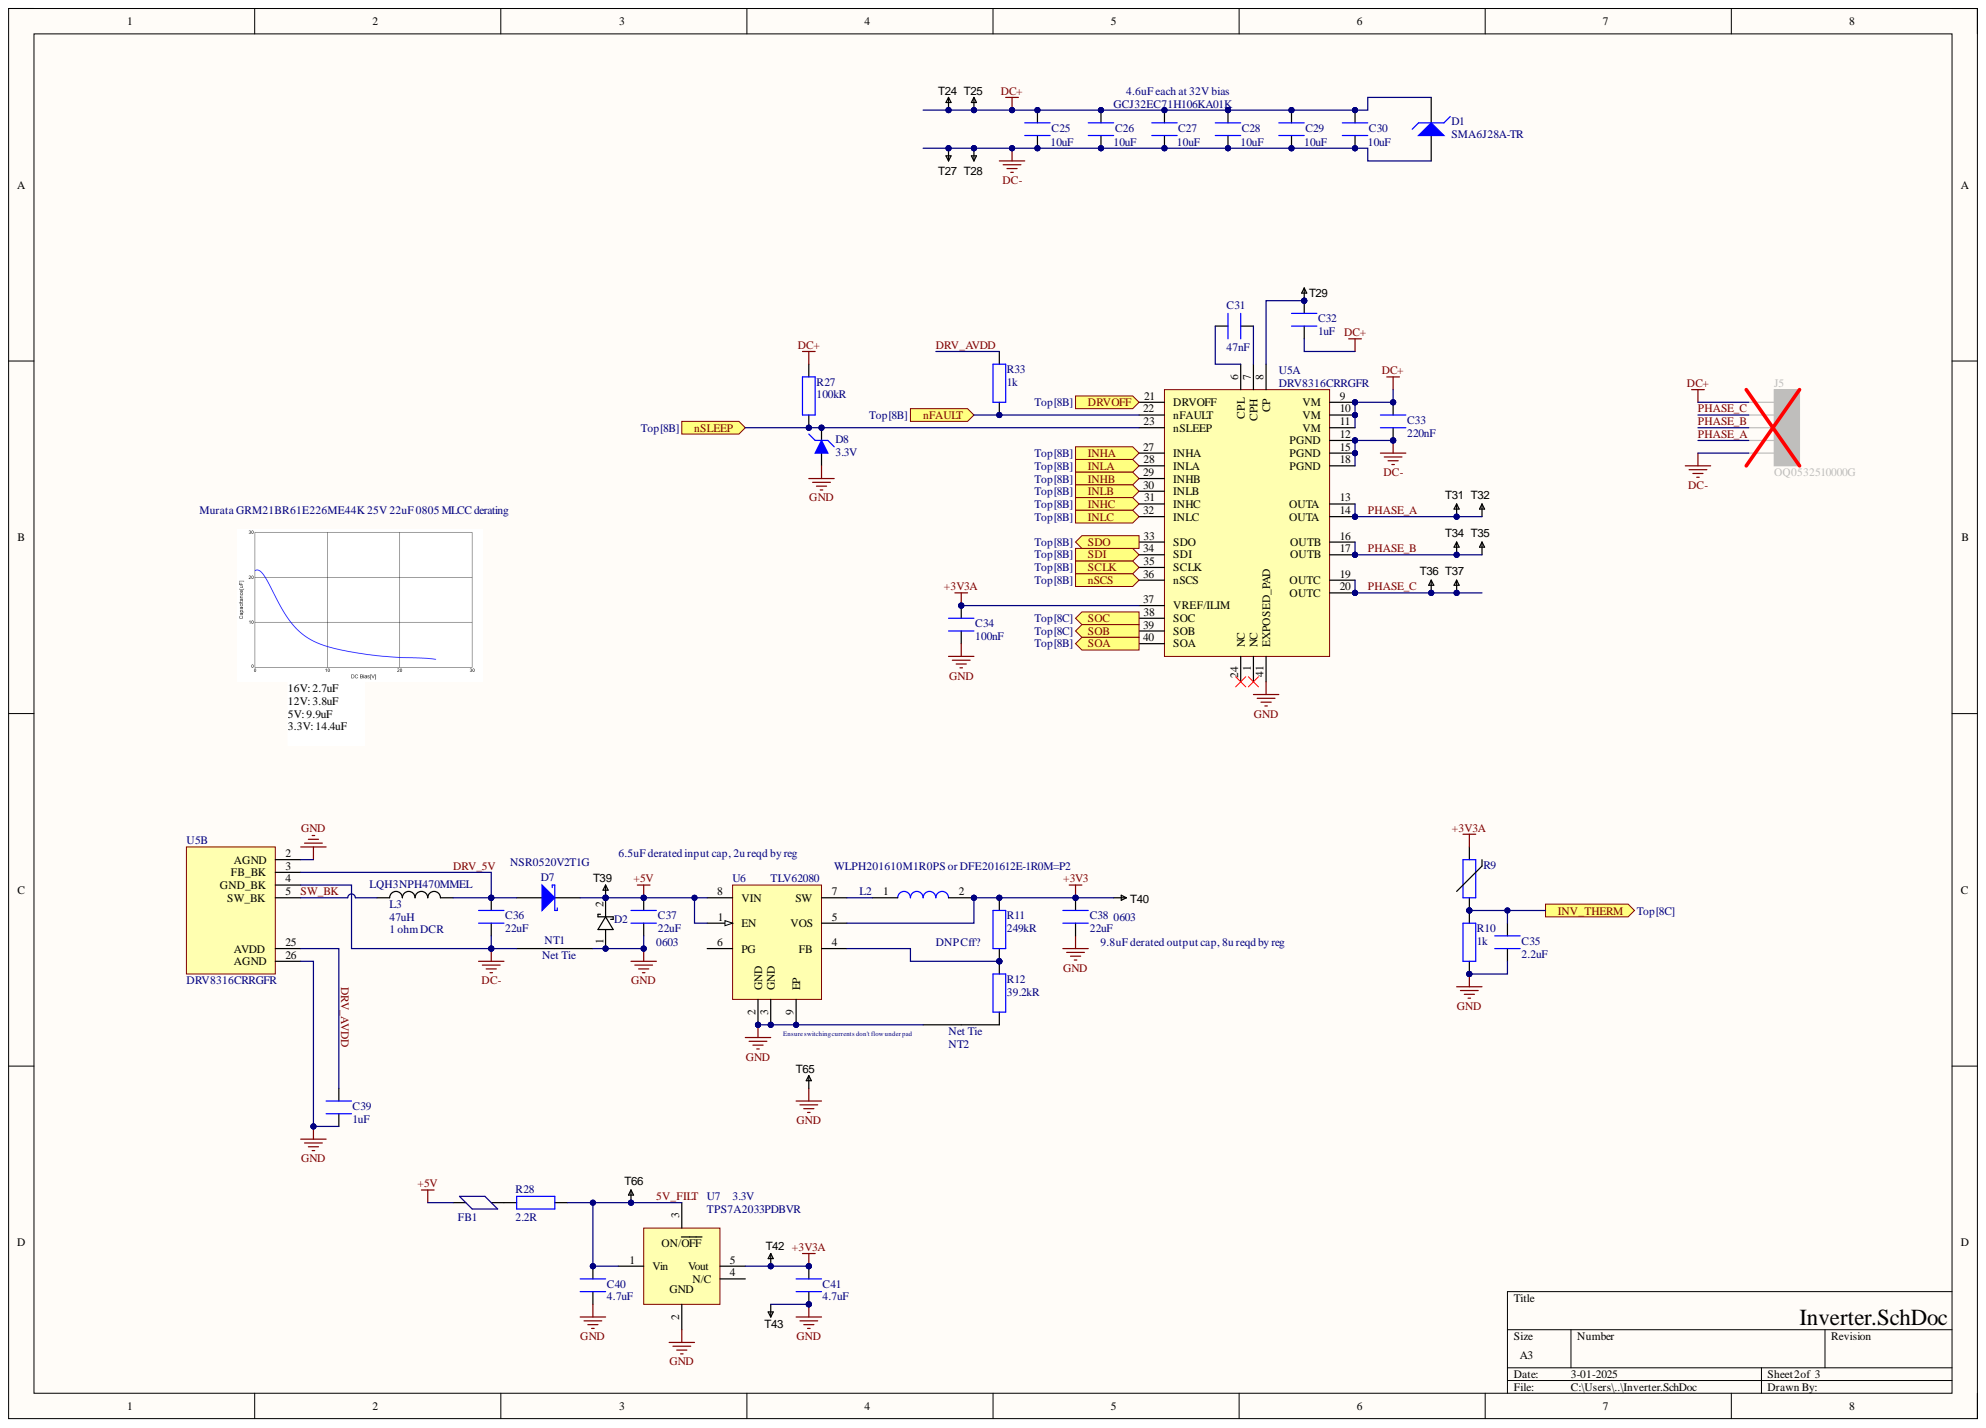
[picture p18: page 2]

6.5uF derated input cap, 2u reqd by reg

9.8uF derated output cap, 8u reqd by reg

Ensure switching currents don't flow under pad

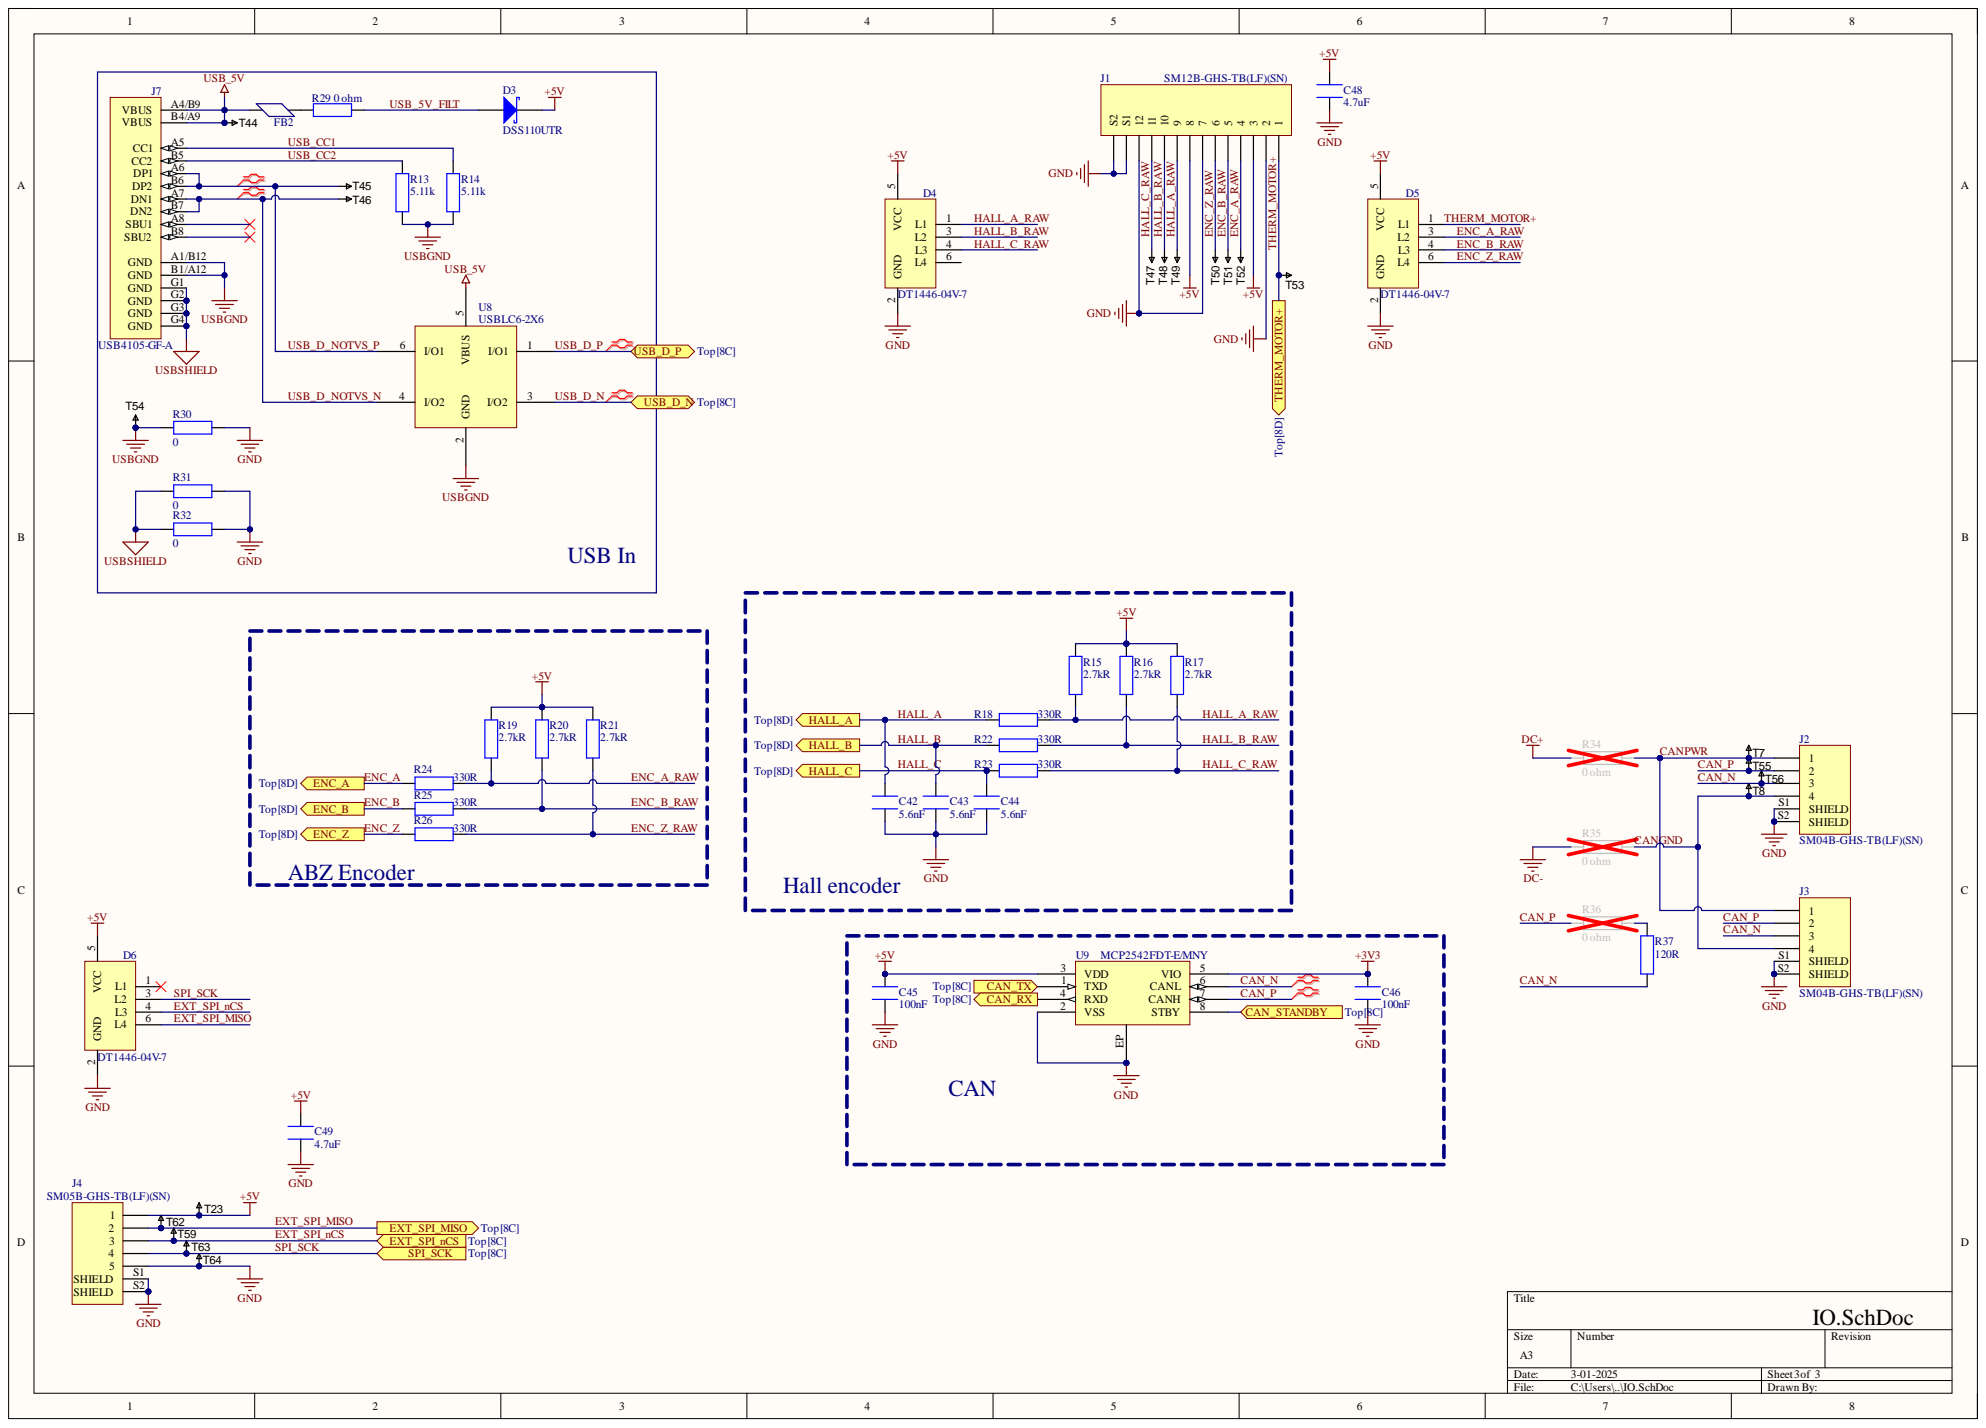
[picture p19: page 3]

HALL_A_RAW

HALL_B | | HALL_B_RAW

SM04B-GHS-TB(LF)(SN)

SM05B-GHS-TB(LF)(SN)

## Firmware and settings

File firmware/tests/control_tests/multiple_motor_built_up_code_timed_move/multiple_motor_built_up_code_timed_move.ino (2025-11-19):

#include <SimpleFOC.h>

#define V_SUPPLY 12
#define motor1_target 2
#define motor2_target 2

#define motor1_vel_limit 5
#define motor1_V_limit 12
#define motor2_vel_limit 5
#define motor2_V_limit 8

BLDCMotor motor1 = BLDCMotor(7);                      //motor phase resistance
BLDCDriver3PWM driver1 = BLDCDriver3PWM(22, 21, 20, 23);  //driver IN1, IN2, IN3, EN pin connections to MCU

MagneticSensorSPI sensor1 = MagneticSensorSPI(32, 14, 0x3FFF);


BLDCMotor motor2 = BLDCMotor(7);                      //motor phase resistance
BLDCDriver3PWM driver2 = BLDCDriver3PWM(18, 17, 16, 19);  //driver IN1, IN2, IN3, EN pin connections to MCU
MagneticSensorSPI sensor2 = MagneticSensorSPI(31, 14, 0x3FFF);



int lastPrintTime = 0;
int i = 0;


void setup() {
  pinMode(36, OUTPUT);  //using pin 23 as another 3.3V source for the motor driver
  digitalWrite(36, HIGH);
  Serial.begin(115200);             // use monitoring with serial
  SimpleFOCDebug::enable(&Serial);  // enable more verbose output for debugging
  motor1.useMonitoring(Serial);
  motor2.useMonitoring(Serial);

  sensor1.init();
  motor1.linkSensor(&sensor1);
  driver1.voltage_power_supply = V_SUPPLY;
  driver1.init();

  motor1.linkDriver(&driver1);  // 3-22-25 updating PID for DRV8302 and MAD motor
  motor1.controller = MotionControlType::angle;
  motor1.foc_modulation = FOCModulationType::SinePWM;
  motor1.PID_velocity.P = 0.1;  // controller configuration based on the control type // too high and motor goes wild
  //motor1.PID_velocity.I = 10;
  //motor1.PID_velocity.D = 0.2;
  //motor1.LPF_velocity.Tf = 0.01;  // velocity low pass filtering time constant
  //motor1.P_angle.P = 20;          // angle loop controller //I am not sure what this is or does
  //motor1.P_angle.I = 1;
  //motor1.P_angle.D = 1;

  //motor1.velocity_limit = motor1_vel_limit;  // angle loop velocity limit
  motor1.voltage_limit = motor1_V_limit;     // default voltage_power_supply

  motor1.init();
  motor1.initFOC();

  motor1.target = motor1_target;  //initial motor position


  //Serial.println("Motor 1 ready");
  _delay(500);

  sensor2.init();
  motor2.linkSensor(&sensor2);
  driver2.voltage_power_supply = V_SUPPLY;
  driver2.init();

  motor2.linkDriver(&driver2);
  motor2.controller = MotionControlType::angle;
  motor2.foc_modulation = FOCModulationType::SinePWM;
  motor2.PID_velocity.P = 0.1;  // .2 controller configuration based on the control type
  //motor2.PID_velocity.I = 20; // 20
  //motor2.PID_velocity.D = .75;  // .5
  //motor2.LPF_velocity.Tf = 0.01;  // .01 velocity low pass filtering time constant
  //motor2.P_angle.P = 20;          // angle loop controller //I am not sure what this is or does
  //motor2.P_angle.I = 1;   // 1
  //motor2.P_angle.D = 1;   // 1

  motor2.velocity_limit = motor2_vel_limit;  // angle loop velocity limit
  motor2.voltage_limit = motor2_V_limit;     // default voltage_power_supply

  motor2.init();
  motor2.initFOC();

  motor2.target = motor2_target;  //initial motor position


  //Serial.println("Motor 2 ready");
  _delay(500);
}

float pos1 = 2;  // previously: 6.28, 5, 2, -2, 5, 12, -3, -8, -5, 1, 10
float pos2 = -2;  // previously 3.14, 4, 1, -1, 4, 10, -2, -10, -4, 0, -10
int loopTime = 5000;

float motor_slow_speed = 15;
float motor_quick_speed = 25;

void loop() {

  while (millis() < ((1 - (motor_slow_speed / motor_quick_speed)) * loopTime)) {
    motor1.velocity_limit = motor_slow_speed;
    motor2.velocity_limit = motor_slow_speed;
    motor1.loopFOC();
    motor2.loopFOC();
    motor1.move(pos1);
    motor2.move(pos1);
  }
  while (millis() >= ((1 - (motor_slow_speed / motor_quick_speed)) * loopTime) && millis() < loopTime) {
    motor1.velocity_limit = motor_quick_speed;
    motor2.velocity_limit = motor_quick_speed;
    motor1.loopFOC();
    motor2.loopFOC();
    motor1.move(pos1);
    motor2.move(pos1);
  }

  while (millis() >= loopTime && millis() < ((1 + (1 - (motor_slow_speed / motor_quick_speed))) * loopTime)) {
    motor1.velocity_limit = motor_slow_speed;
    motor2.velocity_limit = motor_slow_speed;
    motor1.loopFOC();
    motor2.loopFOC();
    motor1.move(pos2);
    motor2.move(pos2);
  }
  while (millis() < ((1 + (1 - (motor_slow_speed / motor_quick_speed))) * loopTime) && millis() < (2 * loopTime)) {
    motor1.velocity_limit = motor_quick_speed;
    motor2.velocity_limit = motor_quick_speed;
    motor1.loopFOC();
    motor2.loopFOC();
    motor1.move(pos2);
    motor2.move(pos2);
  }

  while (millis() >= (2 * loopTime) && millis() < ((2 + (1 - (motor_slow_speed / motor_quick_speed))) * loopTime)) {
    motor1.velocity_limit = motor_slow_speed;
    motor2.velocity_limit = motor_slow_speed;
    motor1.loopFOC();
    motor2.loopFOC();
    motor1.move(pos1);
    motor2.move(pos1);
  }
  while (millis() >= ((2 + (1 - (motor_slow_speed / motor_quick_speed))) * loopTime) && millis() < (3 * loopTime)) {
    motor1.velocity_limit = motor_quick_speed;
    motor2.velocity_limit = motor_quick_speed;
    motor1.loopFOC();
    motor2.loopFOC();
    motor1.move(pos1);
    motor2.move(pos1);
  }

  while (millis() >= (3 * loopTime) && millis() < ((3 + (1 - (motor_slow_speed / motor_quick_speed))) * loopTime)) {
    motor1.velocity_limit = motor_slow_speed;
    motor2.velocity_limit = motor_slow_speed;
    motor1.loopFOC();
    motor2.loopFOC();
    motor1.move(pos2);
    motor2.move(pos2);
  }
  while (millis() >= ((3 + (1 - (motor_slow_speed / motor_quick_speed))) * loopTime) && millis() < (4 * loopTime)) {
    motor1.velocity_limit = motor_quick_speed;
    motor2.velocity_limit = motor_quick_speed;
    motor1.loopFOC();
    motor2.loopFOC();
    motor1.move(pos2);
    motor2.move(pos2);
  }

  while (millis() >= (4 * loopTime) && millis() < ((4 + (1 - (motor_slow_speed / motor_quick_speed))) * loopTime)) {
    motor1.velocity_limit = motor_slow_speed;
    motor2.velocity_limit = motor_slow_speed;
    motor1.loopFOC();
    motor2.loopFOC();
    motor1.move(pos1);
    motor2.move(pos1);
  }
  while (millis() >= ((4 + (1 - (motor_slow_speed / motor_quick_speed))) * loopTime) && millis() < (5 * loopTime)) {
    motor1.velocity_limit = motor_quick_speed;
    motor2.velocity_limit = motor_quick_speed;
    motor1.loopFOC();
    motor2.loopFOC();
    motor1.move(pos1);
    motor2.move(pos1);
  }

  while (millis() >= (5 * loopTime) && millis() < ((5 + (1 - (motor_slow_speed / motor_quick_speed))) * loopTime)) {
    motor1.velocity_limit = motor_slow_speed;
    motor2.velocity_limit = motor_slow_speed;
    motor1.loopFOC();
    motor2.loopFOC();
    motor1.move(pos2);
    motor2.move(pos2);
  }
  while (millis() >= ((5 + (1 - (motor_slow_speed / motor_quick_speed))) * loopTime) && millis() < (6 * loopTime)) {
    motor1.velocity_limit = motor_quick_speed;
    motor2.velocity_limit = motor_quick_speed;
    motor1.loopFOC();
    motor2.loopFOC();
    motor1.move(pos2);
    motor2.move(pos2);
  }

  while (millis() >= (6 * loopTime) && millis() < ((6 + (1 - (motor_slow_speed / motor_quick_speed))) * loopTime)) {
    motor1.velocity_limit = motor_slow_speed;
    motor2.velocity_limit = motor_slow_speed;
    motor1.loopFOC();
    motor2.loopFOC();
    motor1.move(pos1);
    motor2.move(pos1);
  }
  while (millis() >= ((6 + (1 - (motor_slow_speed / motor_quick_speed))) * loopTime) && millis() < (7 * loopTime)) {
    motor1.velocity_limit = motor_quick_speed;
    motor2.velocity_limit = motor_quick_speed;
    motor1.loopFOC();
    motor2.loopFOC();
    motor1.move(pos1);
    motor2.move(pos1);
  }

  while (millis() >= (7 * loopTime) && millis() < ((7 + (1 - (motor_slow_speed / motor_quick_speed))) * loopTime)) {
    motor1.velocity_limit = motor_slow_speed;
    motor2.velocity_limit = motor_slow_speed;
    motor1.loopFOC();
    motor2.loopFOC();
    motor1.move(pos2);
    motor2.move(pos2);
  }
  while (millis() >= ((7 + (1 - (motor_slow_speed / motor_quick_speed))) * loopTime) && millis() < (8 * loopTime)) {
    motor1.velocity_limit = motor_quick_speed;
    motor2.velocity_limit = motor_quick_speed;
    motor1.loopFOC();
    motor2.loopFOC();
    motor1.move(pos2);
    motor2.move(pos2);
  }

  while (millis() >= (8 * loopTime) && millis() < ((8 + (1 - (motor_slow_speed / motor_quick_speed))) * loopTime)) {
    motor1.velocity_limit = motor_slow_speed;
    motor2.velocity_limit = motor_slow_speed;
    motor1.loopFOC();
    motor2.loopFOC();
    motor1.move(pos1);
    motor2.move(pos1);
  }
  while (millis() >= ((8 + (1 - (motor_slow_speed / motor_quick_speed))) * loopTime) && millis() < (9 * loopTime)) {
    motor1.velocity_limit = motor_quick_speed;
    motor2.velocity_limit = motor_quick_speed;
    motor1.loopFOC();
    motor2.loopFOC();
    motor1.move(pos1);
    motor2.move(pos1);
  }

  while (millis() >= (9 * loopTime) && millis() < ((9 + (1 - (motor_slow_speed / motor_quick_speed))) * loopTime)) {
    motor1.velocity_limit = motor_slow_speed;
    motor2.velocity_limit = motor_slow_speed;
    motor1.loopFOC();
    motor2.loopFOC();
    motor1.move(pos2);
    motor2.move(pos2);
  }
  while (millis() >= ((9 + (1 - (motor_slow_speed / motor_quick_speed))) * loopTime) && millis() < (10 * loopTime)) {
    motor1.velocity_limit = motor_quick_speed;
    motor2.velocity_limit = motor_quick_speed;
    motor1.loopFOC();
    motor2.loopFOC();
    motor1.move(pos2);
    motor2.move(pos2);
  }

  while (millis() >= (10 * loopTime) && millis() < ((10 + (1 - (motor_slow_speed / motor_quick_speed))) * loopTime)) {
    motor1.velocity_limit = motor_slow_speed;
    motor2.velocity_limit = motor_slow_speed;
    motor1.loopFOC();
    motor2.loopFOC();
    motor1.move(pos1);
    motor2.move(pos1);
  }
  while (millis() >= ((10 + (1 - (motor_slow_speed / motor_quick_speed))) * loopTime) && millis() < (11 * loopTime)) {
    motor1.velocity_limit = motor_quick_speed;
    motor2.velocity_limit = motor_quick_speed;
    motor1.loopFOC();
    motor2.loopFOC();
    motor1.move(pos1);
    motor2.move(pos1);
  }

  while (millis() >= (11 * loopTime) && millis() < ((11 + (1 - (motor_slow_speed / motor_quick_speed))) * loopTime)) {
    motor1.velocity_limit = motor_slow_speed;
    motor2.velocity_limit = motor_slow_speed;
    motor1.loopFOC();
    motor2.loopFOC();
    motor1.move(pos2);
    motor2.move(pos2);
  }
  while (millis() >= ((11 + (1 - (motor_slow_speed / motor_quick_speed))) * loopTime) && millis() < (12 * loopTime)) {
    motor1.velocity_limit = motor_quick_speed;
    motor2.velocity_limit = motor_quick_speed;
    motor1.loopFOC();
    motor2.loopFOC();
    motor1.move(pos2);
    motor2.move(pos2);
  }

  while ((millis() >= (12 * loopTime)) && i < 1) {
    Serial.print("Motor movement loop completed!");
    //Serial.println(i);
    i++;
    digitalWrite(3, LOW);  // disables all current to motor!!
  }

  /*
  int sinpos1 = 6 * sin(.0005 * millis()) + 4;
  //int sinpos2 = 2 * sin(.0005 * millis()) + 4;
  if (sinpos1 == 3.8) {
   // motor1.move(sinpos1);
    motor2.move(sinpos1);
  }
  if (sinpos1 == .2) {
   // motor1.move(sinpos1);
    motor2.move(sinpos1);
  }
  */

  /*
  if (millis() - lastPrintTime > 2000) {  // Print every 2000ms
    Serial.print("Angle: ");
    Serial.println(sensor1.getAngle());
    Serial.print("Angle: ");
    Serial.println(sensor2.getAngle());
    lastPrintTime = millis();
  }
  */
}

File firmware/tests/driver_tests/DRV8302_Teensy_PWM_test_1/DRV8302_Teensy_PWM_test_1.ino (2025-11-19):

#include <SimpleFOC.h>

#define V_SUPPLY 10
#define motor1_target 2


#define motor1_vel_limit 5
#define motor1_V_limit 12


BLDCMotor motor1 = BLDCMotor(11);                     //motor phase resistance
BLDCDriver3PWM driver1 = BLDCDriver3PWM(0, 1, 2, 3);  //driver IN1, IN2, IN3, EN pin connections to MCU


const int PWM_PIN = 10;
MagneticSensorPWM sensor1 = MagneticSensorPWM(PWM_PIN, 3, 938);  //PWM pin, min pulse, max pulse
void doPWM() {
  sensor1.handlePWM();
}

int lastPrintTime = 0;
int i = 0;

// angle set point variable
float target_angle = 0;
// instantiate the commander
Commander command = Commander(Serial);
void doTarget(char* cmd) {
  command.scalar(&target_angle, cmd);
}

void setup() {
  pinMode(PWM_PIN, INPUT);          //using pin 23 as another 3.3V source for the motor driver
  Serial.begin(115200);             // use monitoring with serial
  SimpleFOCDebug::enable(&Serial);  // enable more verbose output for debugging
  motor1.useMonitoring(Serial);
  motor1.monitor_downsample = 10;  // monitor motor angle
  sensor1.init();
  sensor1.enableInterrupt(doPWM);

  motor1.linkSensor(&sensor1);
  driver1.voltage_power_supply = V_SUPPLY;
  driver1.init();

  motor1.linkDriver(&driver1);  // 3-22-25 updating PID for DRV8302 and MAD motor
  motor1.controller = MotionControlType::angle;
  motor1.foc_modulation = FOCModulationType::SinePWM;

  // velocity PI controller parameters
  motor1.PID_velocity.P = 0.2f;
  motor1.PID_velocity.I = 20;
  motor1.PID_velocity.D = 0;
  // maximal voltage to be set to the motor
  motor1.voltage_limit = 6;

  // velocity low pass filtering time constant
  // the lower the less filtered
  motor1.LPF_velocity.Tf = 0.01f;

  // angle P controller
  motor1.P_angle.P = 20;

  //motor1.velocity_limit = motor1_vel_limit;  // angle loop velocity limit
  motor1.voltage_limit = motor1_V_limit;  // default voltage_power_supply
  motor1.init();
  motor1.initFOC();
  motor1.target = motor1_target;  //initial motor position
  command.add('T', doTarget, "target angle");

  Serial.println(F("Motor ready."));
  Serial.println(F("Set the target angle using serial terminal:"));

  //Serial.println("Motor 1 ready");
  _delay(500);
}


float pos1 = 4;       // previously: 6.28, 5, 2, -2, 5, 12, -3, -8, -5, 1, 10, 20
float pos2 = 16;      // previously 3.14, 4, 1, -1, 4, 10, -2, -10, -4, 0, -10, -20
int loopTime = 2000;  //previously: 5000

float motor_slow_speed = 20;
float motor_quick_speed = 40;

void loop() {


  // main FOC algorithm function
  // the faster you run this function the better
  // Arduino UNO loop  ~1kHz
  // Bluepill loop ~10kHz
  motor1.loopFOC();

  // Motion control function
  // velocity, position or voltage (defined in motor.controller)
  // this function can be run at much lower frequency than loopFOC() function
  // You can also use motor.move() and set the motor.target in the code
  motor1.move(target_angle);


  // function intended to be used with serial plotter to monitor motor variables
  // significantly slowing the execution down!!!!
  // motor.monitor();

  // user communication
  command.run();


  /*
  while (millis() < ((1 - (motor_slow_speed / motor_quick_speed)) * loopTime)) {
    motor1.velocity_limit = motor_slow_speed;
    motor1.loopFOC();
    motor1.move(pos1);
  }
  while (millis() >= ((1 - (motor_slow_speed / motor_quick_speed)) * loopTime) && millis() < loopTime) {
    motor1.velocity_limit = motor_quick_speed;
    motor1.loopFOC();
    motor1.move(pos2);
  }

  while (millis() >= loopTime && millis() < ((1 + (1 - (motor_slow_speed / motor_quick_speed))) * loopTime)) {
    motor1.velocity_limit = motor_slow_speed;
    motor1.loopFOC();
    motor1.move(pos1);
  }
  while (millis() < ((1 + (1 - (motor_slow_speed / motor_quick_speed))) * loopTime) && millis() < (2 * loopTime)) {
    motor1.velocity_limit = motor_quick_speed;
    motor1.loopFOC();
    motor1.move(pos2);
  }

  while (millis() >= (2 * loopTime) && millis() < ((2 + (1 - (motor_slow_speed / motor_quick_speed))) * loopTime)) {
    motor1.velocity_limit = motor_slow_speed;
    motor1.loopFOC();
    motor1.move(pos1);
  }
  while (millis() >= ((2 + (1 - (motor_slow_speed / motor_quick_speed))) * loopTime) && millis() < (3 * loopTime)) {
    motor1.velocity_limit = motor_quick_speed;
    motor1.loopFOC();
    motor1.move(pos2);
  }

  while (millis() >= (3 * loopTime) && millis() < ((3 + (1 - (motor_slow_speed / motor_quick_speed))) * loopTime)) {
    motor1.velocity_limit = motor_slow_speed;
    motor1.loopFOC();
    motor1.move(pos1);
  }
  while (millis() >= ((3 + (1 - (motor_slow_speed / motor_quick_speed))) * loopTime) && millis() < (4 * loopTime)) {
    motor1.velocity_limit = motor_quick_speed;
    motor1.loopFOC();
    motor1.move(pos2);
  }

  while (millis() >= (4 * loopTime) && millis() < ((4 + (1 - (motor_slow_speed / motor_quick_speed))) * loopTime)) {
    motor1.velocity_limit = motor_slow_speed;
    motor1.loopFOC();
    motor1.move(pos1);
  }
  while (millis() >= ((4 + (1 - (motor_slow_speed / motor_quick_speed))) * loopTime) && millis() < (5 * loopTime)) {
    motor1.velocity_limit = motor_quick_speed;
    motor1.loopFOC();
    motor1.move(pos2);
  }

  while (millis() >= (5 * loopTime) && millis() < ((5 + (1 - (motor_slow_speed / motor_quick_speed))) * loopTime)) {
    motor1.velocity_limit = motor_slow_speed;
    motor1.loopFOC();
    motor1.move(pos1);
  }
  while (millis() >= ((5 + (1 - (motor_slow_speed / motor_quick_speed))) * loopTime) && millis() < (6 * loopTime)) {
    motor1.velocity_limit = motor_quick_speed;
    motor1.loopFOC();
    motor1.move(pos2);
  }

  while (millis() >= (6 * loopTime) && millis() < ((6 + (1 - (motor_slow_speed / motor_quick_speed))) * loopTime)) {
    motor1.velocity_limit = motor_slow_speed;
    motor1.loopFOC();
    motor1.move(pos1);
  }
  while (millis() >= ((6 + (1 - (motor_slow_speed / motor_quick_speed))) * loopTime) && millis() < (7 * loopTime)) {
    motor1.velocity_limit = motor_quick_speed;
    motor1.loopFOC();
    motor1.move(pos2);
  }

  while (millis() >= (7 * loopTime) && millis() < ((7 + (1 - (motor_slow_speed / motor_quick_speed))) * loopTime)) {
    motor1.velocity_limit = motor_slow_speed;
    motor1.loopFOC();
    motor1.move(pos1);
  }
  while (millis() >= ((7 + (1 - (motor_slow_speed / motor_quick_speed))) * loopTime) && millis() < (8 * loopTime)) {
    motor1.velocity_limit = motor_quick_speed;
    motor1.loopFOC();
    motor1.move(pos2);
  }

  while (millis() >= (8 * loopTime) && millis() < ((8 + (1 - (motor_slow_speed / motor_quick_speed))) * loopTime)) {
    motor1.velocity_limit = motor_slow_speed;
    motor1.loopFOC();
    motor1.move(pos1);
  }
  while (millis() >= ((8 + (1 - (motor_slow_speed / motor_quick_speed))) * loopTime) && millis() < (9 * loopTime)) {
    motor1.velocity_limit = motor_quick_speed;
    motor1.loopFOC();
    motor1.move(pos2);
  }
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

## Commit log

2025-01-30 Added .STEP file for the Nvidia Jetson Nano board and changed the license wording in the README.md file.
2025-01-30 Revert "Added .STEP file for the Nvidia Jetson Nano board and changed the license wording in the README.md file."
    This reverts commit 95083d1c199bfb8f5f54fe240bfbd90db571ed1f.
2025-01-30 Added the .STEP file for the Nvidia jetson Nano.
2025-02-06 Added hardware documentation and verified working test programs for teh Teensy4.0+SimpleFOC mini+AS5047p adapterboard setup.
2025-02-06 Upload circuit used for BLDC_motor_SimpleFOC_angle_control_teensy4.0_test.
2025-02-06 UPdated Teensy4.0 SImplFOC angle control code.
2025-02-18 Uploaded code for multiple motor control.
2025-02-19 Updated working CAN bus tests.
2025-03-10 Updated movement loop and set PID values to default.
2025-03-19 Manual for STM32 based driver alternative.
2025-06-27 Uploaded pinout for plug for AS5047P encoder.
2025-09-23 Upload block diagram for custom all-in-one controller, driver, encoder board.
2025-10-09 First iteration of custom driver and encoder.
2026-02-16 STM32 ESC pcb files
2026-04-28 added odrive schematic for reference for DRIVER REV3
2026-06-20 changed folder name to schematic
2026-06-21 finished V1 of isolated test boards for driver, encoder, MCU
2026-06-22 REV1 of all boards complete
    [BLDC_complete_drive_controller_REV1_BOM.ods]
2026-06-22 old docs from work PC
    [BOM_DRV_8316_AMS5600_V1.xlsx, DRV8316_V1_top_paste.dxf, DRV_8316_Top-Paste-Mask-Layer.dxf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]
2026-06-25 kicad project files
    [ProPrj_BLDC_complete_drive_controller_REV2_2026-06-24.kicad_pcb, ProPrj_BLDC_complete_drive_controller_REV2_2026-06-24.kicad_sch]
2026-06-27 starting CAN tests on jetson
2026-06-27 esp32s3 CAN bus circuitpython code copy
    [ProPrj_BLDC_complete_drive_controller_REV2_2026-06-24.kicad_pcb, ProPrj_BLDC_complete_drive_controller_REV2_2026-06-24.kicad_sch]
2026-06-28 working simple test of esp32s3 CAN listen
    [BOM_complete_drive_controller_REV2.xlsx]
2026-06-29 trying to update the simple CAN bus python sender
2026-06-29 restructured project folders
    [BLDC_complete_drive_controller_REV1_BOM.ods, BOM_DRV_8316_AMS5600_V1.xlsx, BOM_complete_drive_controller_REV2.xlsx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]
2026-06-30 reorg, made an arduino library for custom STM32 pins
    [BLDC_complete_drive_controller_REV1_BOM.ods, BOM_DRV_8316_AMS5600_V1.xlsx, BOM_complete_drive_controller_REV2.xlsx]
